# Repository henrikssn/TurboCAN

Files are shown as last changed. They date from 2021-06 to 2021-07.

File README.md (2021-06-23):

# TurboCAN

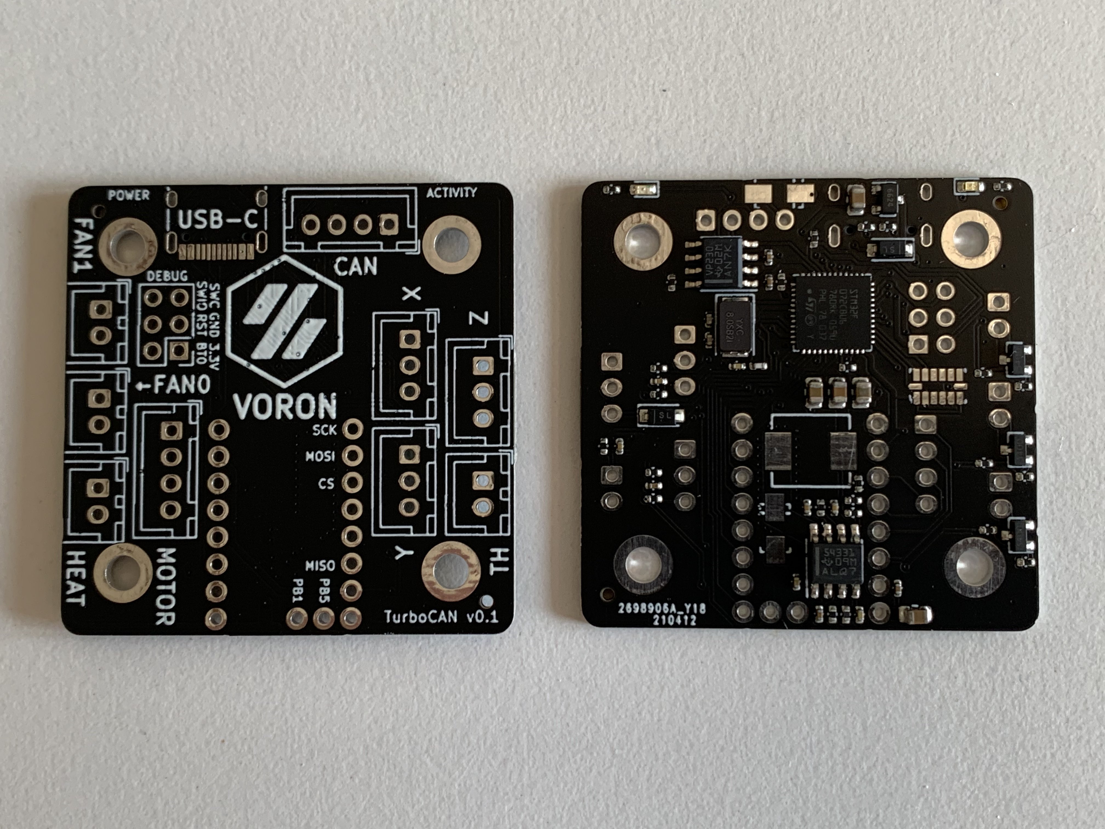
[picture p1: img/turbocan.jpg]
Image of TurboCAN board


This is the official repository for the TurboCAN controller board, designed specifically for the [Voron AfterBurner] toolhead but can also be used on similar toolheads using NEMA17 steppers. The main benefit of this board is the capability to run the toolhead over just 4 wires (CAN, +24V, Ground) which greatly simplifies the wiring in the Voron v1 and v2 models.

[Voron AfterBurner]: https://github.com/VoronDesign/Voron-Afterburner

## Features

* 1x Combined CAN-bus and 24V power port with polarity protection
* 1x ADXL345 accelerometer for use with Klipper's input shaper feature
* 1x 24V stepper stick mount and motor output
* 3x 24V MOSFET fan0/fan1/heater outputs (up to 3A)
* 2x 5V powered endstop inputs (marked X/Y), could be used for toolhead mounted endstops (microswitch or hall effect), filament runout sensor or 5V Z probe.
* 1x 24V powered endstop input (marked Z) with built-in BAT42 diode, used for inductive probe on the AfterBurner but also supports microswitch based probing (e.g. Magprobe).
* 1x Thermistor input with 4.7k pullup resistor
* 1x USB-C port
* 1x SWD debug port with BOOT0/RESET broken out
* 5V 3A buck converter (available externally on X/Y endstops) and 3.3V 200mA linear regulator (internal only)
* Power LED & Activity (PA1) LED

The board supports interfacing with Klipper both over CAN and USB-C (selectable when building the Klipper firmware).

## Use cases

The TurboCAN board is actually not only useful as a toolhead board, here are some reasons why you want more of them:

* Want even less wiring? TurboCAN fits on the back of any NEMA17 stepper, so you can mount TurboCAN boards on e.g. the A/B (or X/Y) steppers and run them over a shared CAN bus.
* Need a USB to CAN interface? TurboCAN can do USB and CAN at the same time, so you can flash CandleLight firmware and use it as a USB-CAN interface.
* Want input shaper but annoyed by the complicated SPI wiring needed for the ADXL345 board? Just use a spare TurboCAN board over USB(/CAN) instead.

## Current status

**WARNING:** While the author has a working printer running a TurboCAN v0.1 board, this project is in early development, and most likely still has undiscovered issues. Build one at your own risk!

- [x] v0.1 boards ordered
- [x] v0.1 boards testing
  - [x] LEDs
  - [x] 3.3v LDO
  - [x] SWD debug port
  - [x] USB interface
  - [x] Buck converter
  - [x] Stepper stick
  - [x] MOSFET outputs
  - [x] CAN-bus + Flashing Klipper (CAN)
  - [x] Thermistor input
  - [x] X/Y endstop inputs
  - [x] Z endstop input

## Getting started

1. Configure Klipper using `make menuconfig`:

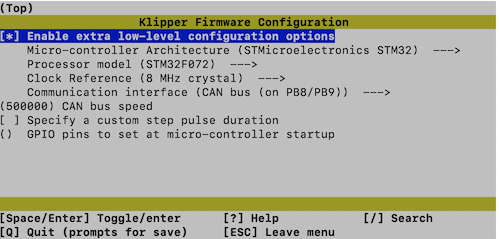
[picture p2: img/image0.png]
Klipper menuconfig


2. Put a jumper between `BOOT0` and `3.3V` and power cycle the board.

3. Flash the TurboCAN board using `make flash FLASH_DEVICE=1234:ABCD` (replace USB vendor/product, you find them with `lsusb`).

4. Connect the TurboCAN board using your favorite CAN bus interface (or use another TurboCAN board, see below).

5. Run the `klipper/scripts/canbus_query.py` command to determine the CAN address. See [Klipper docs](https://www.klipper3d.org/CANBUS.html) for more info.

6. Use the [provided Klipper config](klipper/turbocan.cfg) as a starting point.

## Changelog

### v0.2

* Errata fixes
  * LEDs are now mounted the right way.
  * R11 connected to R10/VSENSE.
  * SPI bus to the ADXL345 now have MISO/MOSI on the right pins.
  * Z probe input now has filtering and pullup resistor.
  * Reworked buck converter compensation circuitry.
  * Added CAN termination resistor.
* Added 100uF bulk capacitor for 24V to mitigate voltage fluctuations due to long cables.
* Thermistor resistor is now in 0805 package (was 0402) to simplify replacement to 1k (for PT1000 sensor).
* Improved filtering of analog power domain to reduce ADC noise.
* Replaced the heater mosfet with a more powerful AON7400A.
* Replaced the +3.3V connection to MS1 with an unpopulated resistor to give the board UART address 0 by default.
* Added optional pullup resistors to MS2/SPREAD to support standalone mode for the step stick.

## Errata

### v0.1

* LEDs are mounted backwards.
  * Workaround: Reverse them (or simply skip, they aren't essential).
* R11 not connected to R10/VSENSE.
  * Workaround: Simple to bodge as R10 is next to it.
* MISO and MOSI are swapped on the SPI bus to the ADXL345.
  * Workaround: Use software SPI.
* Z probe input lacks filtering and pullup resistor
  * Workaround: Use MCU internal pullup.
* Higher than optimal noise from the buck converter leading to noisy accelerometer readings.
  * Workaround: Doesn't need one, performance is still good enough for input shaper.
* No CAN termination resistors on-board
  * Workaround: Mount a 0603 120Ohm resistor between the H/L legs of the CAN JST-XH connector on each end of the bus.
* Thermistor readings are noisy (fluctuating 2-3C) with a PT1000 sensor
  * Workaround: Use a B3950 or replace the pullup resistor with a 1k 0.5%

## Developer Info

### Generating fabrication outputs for JLCPCB

1. Export Gerbers and drill file from pcbnew, make a zip file out of these.
2. Generate a BOM csv using `bom_csv_jlcpcb.py` from [kicad-jlcpcb-bom-plugin].
3. Generate a CPL file from pcbnew.
4. Convert the CPL file to JLCPCB format using  using `kicad_pos_to_cpl.py` from [kicad-jlcpcb-bom-plugin].

[kicad-jlcpcb-bom-plugin]: https://github.com/wokwi/kicad-jlcpcb-bom-plugin
## Attribution

Although this was designed from scratch, it was inspired by the [Huvud] board made by Pontus Borg.

[Huvud]: https://github.com/bondus/KlipperToolboard

## License

For compability with other Voron projects, all included files are licensed under the [GNU GPL-3 license].

[GNU GPL-3 license]: https://www.gnu.org/licenses/gpl-3.0.html

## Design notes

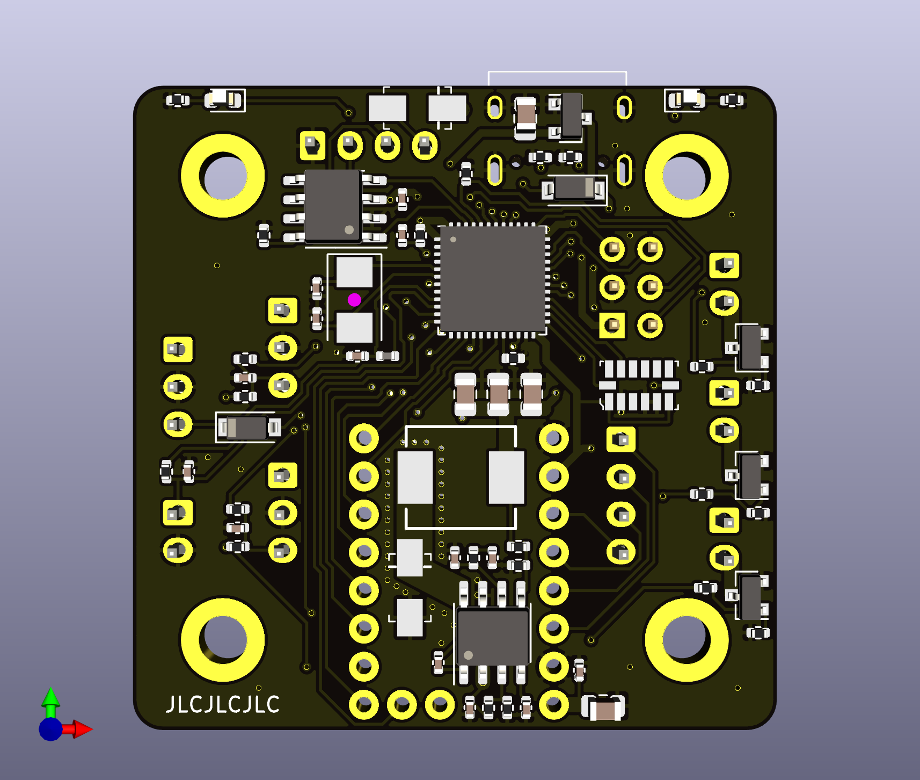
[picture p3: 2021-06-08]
hardware/png/turbocan-front.png

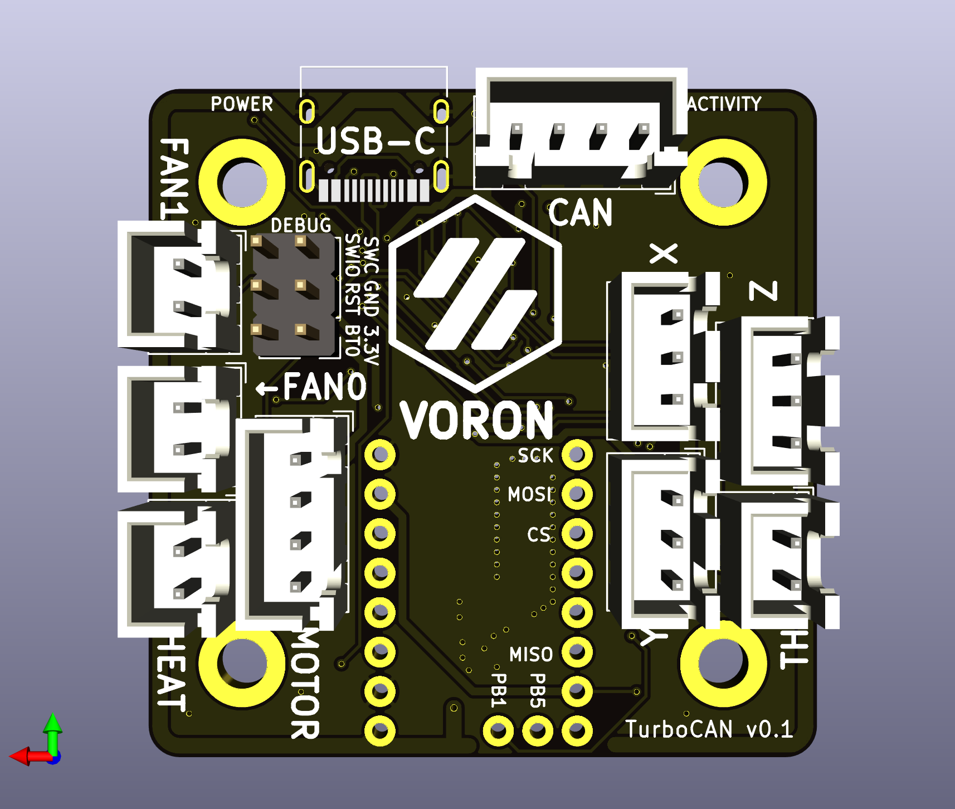
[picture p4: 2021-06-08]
hardware/png/turbocan-back.png

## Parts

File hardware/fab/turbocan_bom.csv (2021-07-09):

Comment | Designator | Footprint | LCSC Part #
10uF | C1,C5 | C_0805_2012Metric | C15850
100nF | C2,C3,C4,C9,C10,C11,C12,C17,C20,C22 | C_0402_1005Metric | C1525
10nF | C6,C19 | C_0402_1005Metric | C15195
1nF | C7 | C_0402_1005Metric | C1523
1pF | C8 | C_0402_1005Metric | C1550
22uF | C13,C14,C15 | C_0805_2012Metric | C45783
12pF | C16,C18 | C_0402_1005Metric | C1547
100uF | C21 | CP_Elec_8x10 | C59944
1uF | C23 | C_0402_1005Metric | C52923
BAT42W-V | D1 | D_SOD-123 | C8598
SS54 | D2,D3 | DO-214AC | C22452
BAT42W | D4 | D_SOD-123 | C8598
LED_Red | D5 | LED_0603_1608Metric | C2286
LED_Green | D6 | LED_0603_1608Metric | C72043
MountingHole | H1,H2,H3,H4 | MountingHole_3.2mm_M3_DIN965_Pad
USB_C_Receptacle_USB2.0 | J1 | USB_C_Receptacle_HRO_TYPE-C-31-M-12
STEPPER | J2 | JST_XH_B4B-XH-A_1x04_P2.50mm_Vertical
DEBUG | J5 | PinHeader_2x03_P2.54mm_Vertical
ENDSTOPX | J7 | JST_XH_B3B-XH-A_1x03_P2.50mm_Vertical
ENDSTOPY | J8 | JST_XH_B3B-XH-A_1x03_P2.50mm_Vertical
TH0 | J9 | JST_XH_B2B-XH-A_1x02_P2.50mm_Vertical
CAN_PORT | J10 | JST_XH_B4B-XH-A_1x04_P2.50mm_Vertical
FAN0 | J11 | JST_XH_B2B-XH-A_1x02_P2.50mm_Vertical
FAN1 | J12 | JST_XH_B2B-XH-A_1x02_P2.50mm_Vertical
HEAT | J13 | JST_XH_B2B-XH-A_1x02_P2.50mm_Vertical
PROBE | J14 | JST_XH_B3B-XH-A_1x03_P2.50mm_Vertical
6.8uH | L1 | L_SMD_7.3x6.8 | C207841
Ferrite bead | L2,L3 | L_0805_2012Metric | C1017
5.1k | R1,R2 | R_0402_1005Metric | C25905
1k | R3,R12,R13,R23,R24,R28 | R_0402_1005Metric | C11702
330k | R4 | R_0402_1005Metric | C25778
68k | R5,R6 | R_0402_1005Metric | C36871
10k | R7,R8,R10,R14,R15,R16,R20,R21,R22,R27 | R_0402_1005Metric | C25744
4.7k | R9 | R_0805_2012Metric | C17673
1.2k | R11 | R_0402_1005Metric | C25862
100 | R17,R18,R19 | R_0402_1005Metric | C25076
680 | R25 | R_0402_1005Metric | C25130
120Ohm | R26 | R_0805_2012Metric | C17437
DNP | R29,R30,R31 | R_0402_1005Metric
AP2127N-3.3 | U1 | SOT-23 | C5446
TMC2209StepStick | U2 | TMC2209StepStick
SN65HVD230 | U3 | SOIC-8_3.9x4.9mm_P1.27mm | C12084
TPS54331 | U4 | SOIC-8_3.9x4.9mm_P1.27mm | C9865
AO3400A | U5,U6 | SOT-23 | C344010
AON7400A | U7 | DFN-8-1EP_3x3mm_P0.65mm_EP1.7x2.05mm | C85734
STM32F072CBUx | U8 | QFN-48-1EP_7x7mm_P0.5mm_EP5.6x5.6mm | C92504
ADXL345BCCZ | U9 | LGA-14_3x5mm_RevA | C9667
Crystal | Y1 | Crystal_SMD_5032-2Pin_5.0x3.2mm | C115962

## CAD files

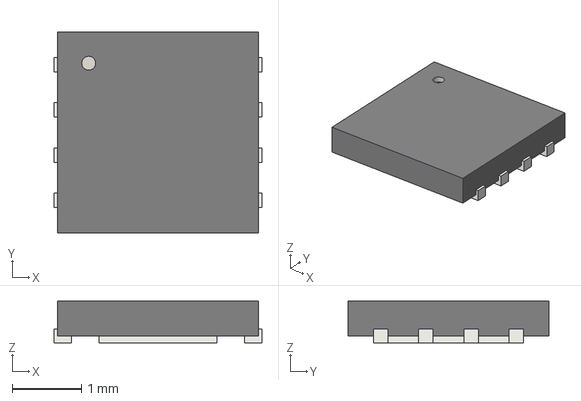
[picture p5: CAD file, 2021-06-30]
hardware/shapes3D/DFN-8-1EP_3x3mm_P0.65mm_EP1.7x2.05mm.step
3.00 x 2.90 x 0.6 mm

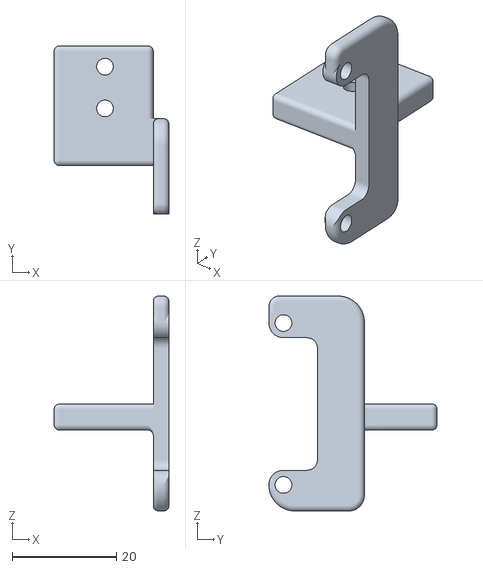
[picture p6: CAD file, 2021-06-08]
STL/Chain Anchor High.stl
22.0 x 32.2 x 41.2

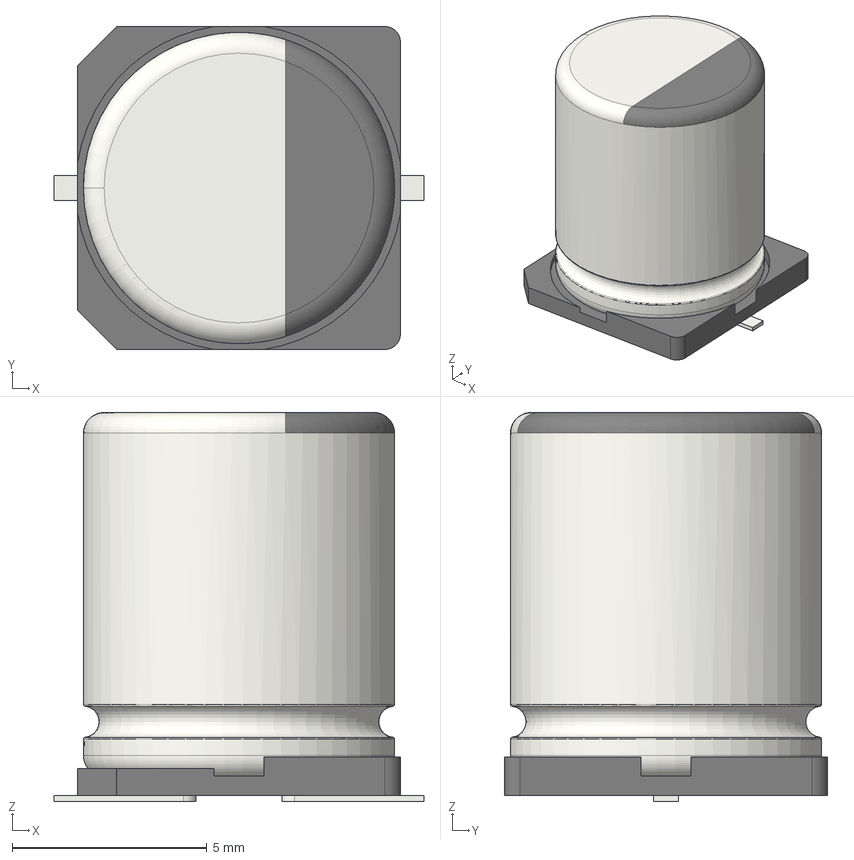
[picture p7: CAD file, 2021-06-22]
hardware/shapes3D/CP_Elec_8x10.step
9.50 x 8.30 x 10.0 mm

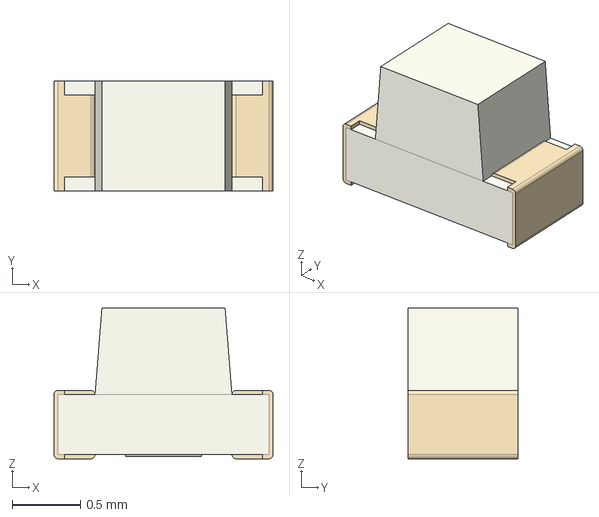
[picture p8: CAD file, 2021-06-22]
hardware/shapes3D/LED_0603_1608Metric.step
1.60 x 0.8 x 1.10 mm

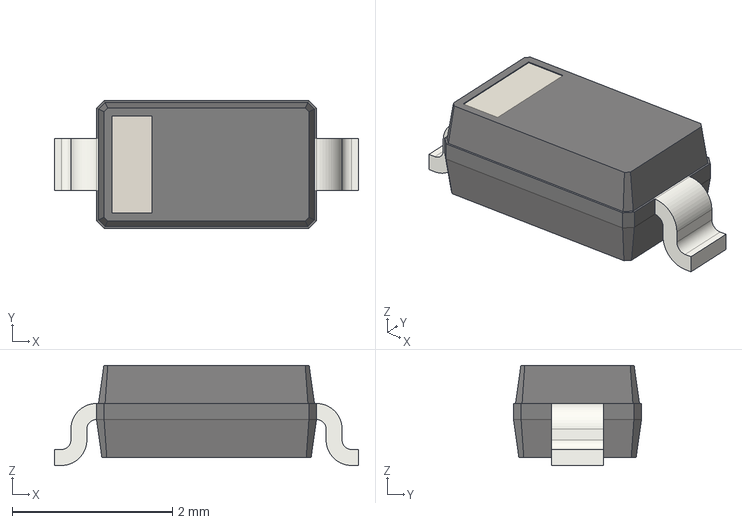
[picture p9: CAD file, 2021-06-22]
hardware/shapes3D/D_SOD-123.step
3.80 x 1.60 x 1.25 mm

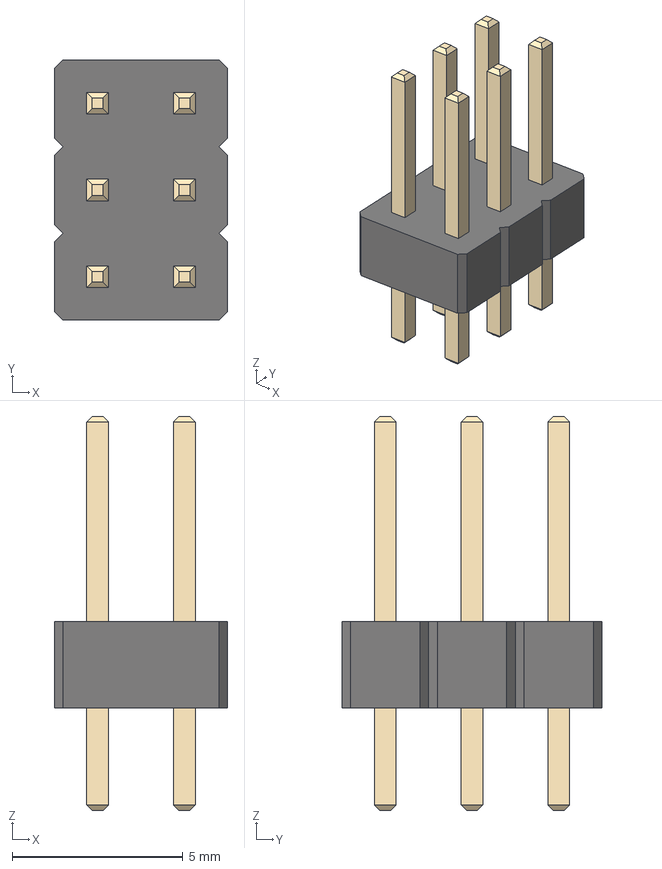
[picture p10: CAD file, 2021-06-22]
hardware/shapes3D/PinHeader_2x03_P2.54mm_Vertical.step
5.08 x 7.62 x 11.5 mm

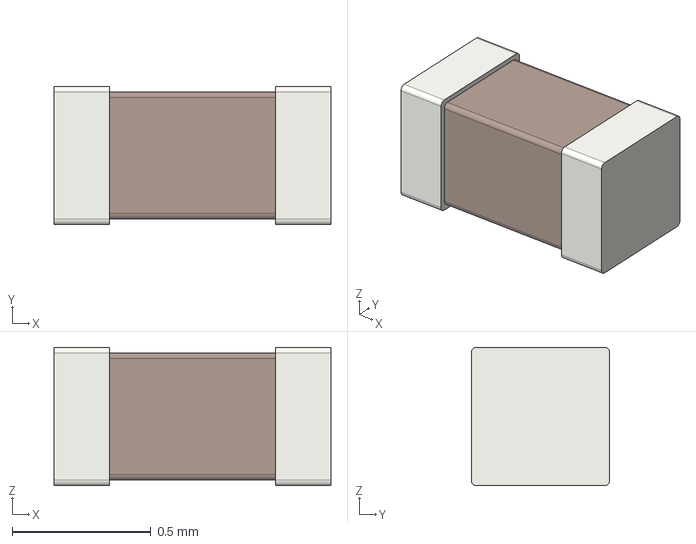
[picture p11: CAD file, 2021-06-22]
hardware/shapes3D/C_0402_1005Metric.step
1.00 x 0.5 x 0.5 mm

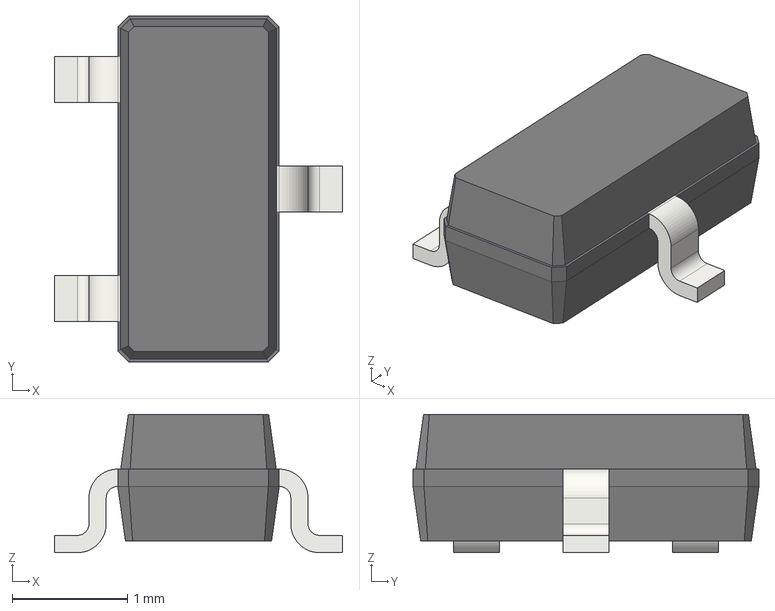
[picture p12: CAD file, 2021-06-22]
hardware/shapes3D/SOT-23.step
2.50 x 3.00 x 1.20 mm

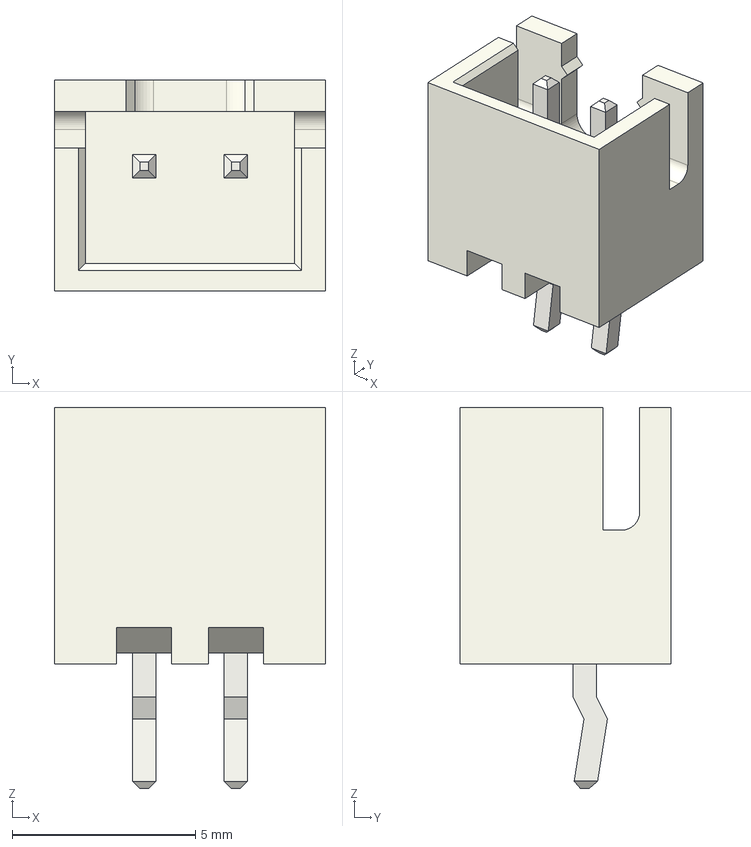
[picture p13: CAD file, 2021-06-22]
hardware/shapes3D/JST_XH_B2B-XH-A_1x02_P2.50mm_Vertical.step
7.40 x 5.75 x 10.4 mm

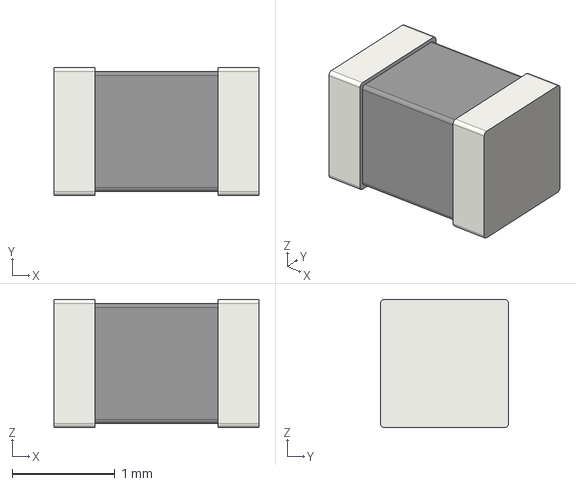
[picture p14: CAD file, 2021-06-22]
hardware/shapes3D/L_0805_2012Metric.step
2.00 x 1.25 x 1.25 mm

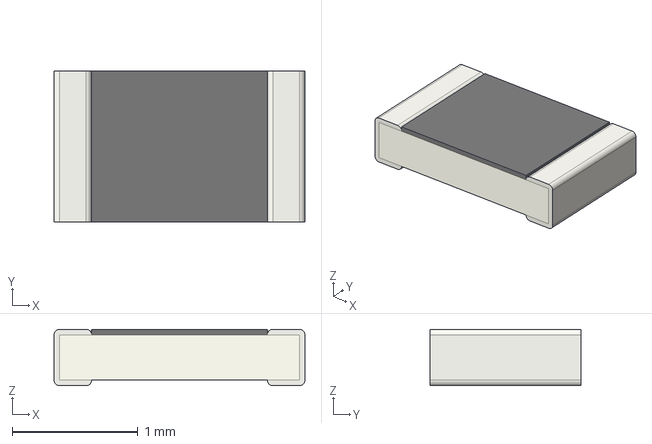
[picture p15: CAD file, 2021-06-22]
hardware/shapes3D/R_0805_2012Metric.step
2.00 x 1.20 x 0.45 mm

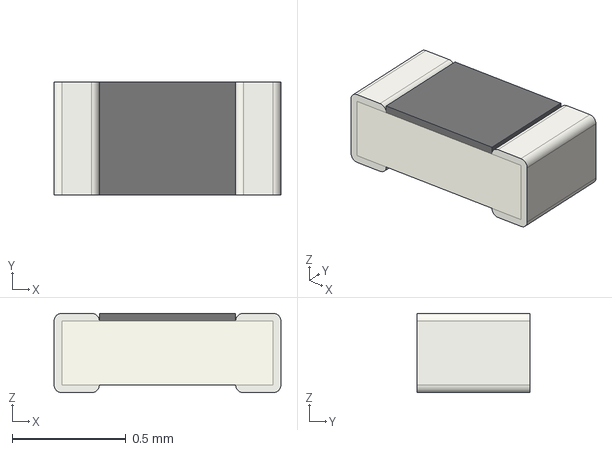
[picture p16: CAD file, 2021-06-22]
hardware/shapes3D/R_0402_1005Metric.step
1.00 x 0.5 x 0.35 mm

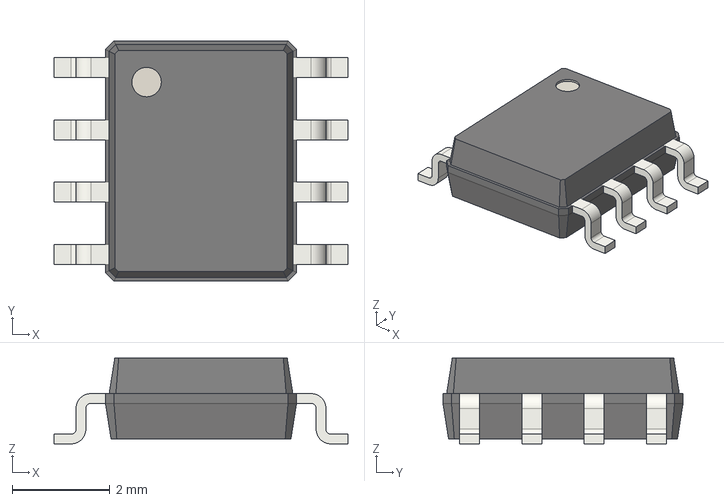
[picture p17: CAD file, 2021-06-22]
hardware/shapes3D/SOIC-8_3.9x4.9mm_P1.27mm.step
6.00 x 4.90 x 1.75 mm

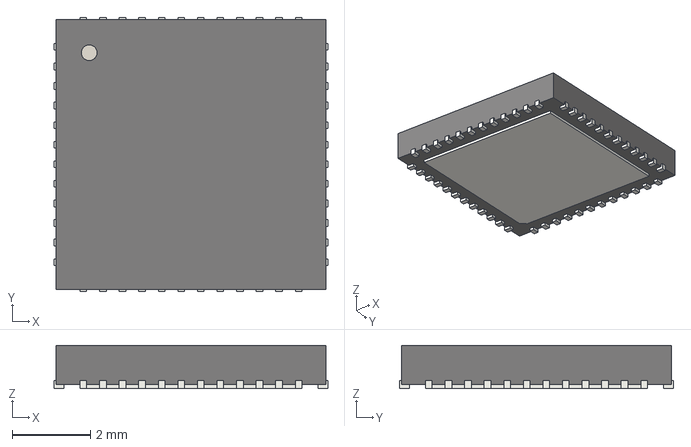
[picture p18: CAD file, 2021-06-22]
hardware/shapes3D/QFN-48-1EP_7x7mm_P0.5mm_EP5.6x5.6mm.step
7.00 x 7.00 x 1.10 mm

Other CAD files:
hardware/shapes3D/JST_XH_B4B-XH-A_1x04_P2.50mm_Vertical.step
hardware/shapes3D/JST_XH_B3B-XH-A_1x03_P2.50mm_Vertical.step
hardware/shapes3D/C_0805_2012Metric.step

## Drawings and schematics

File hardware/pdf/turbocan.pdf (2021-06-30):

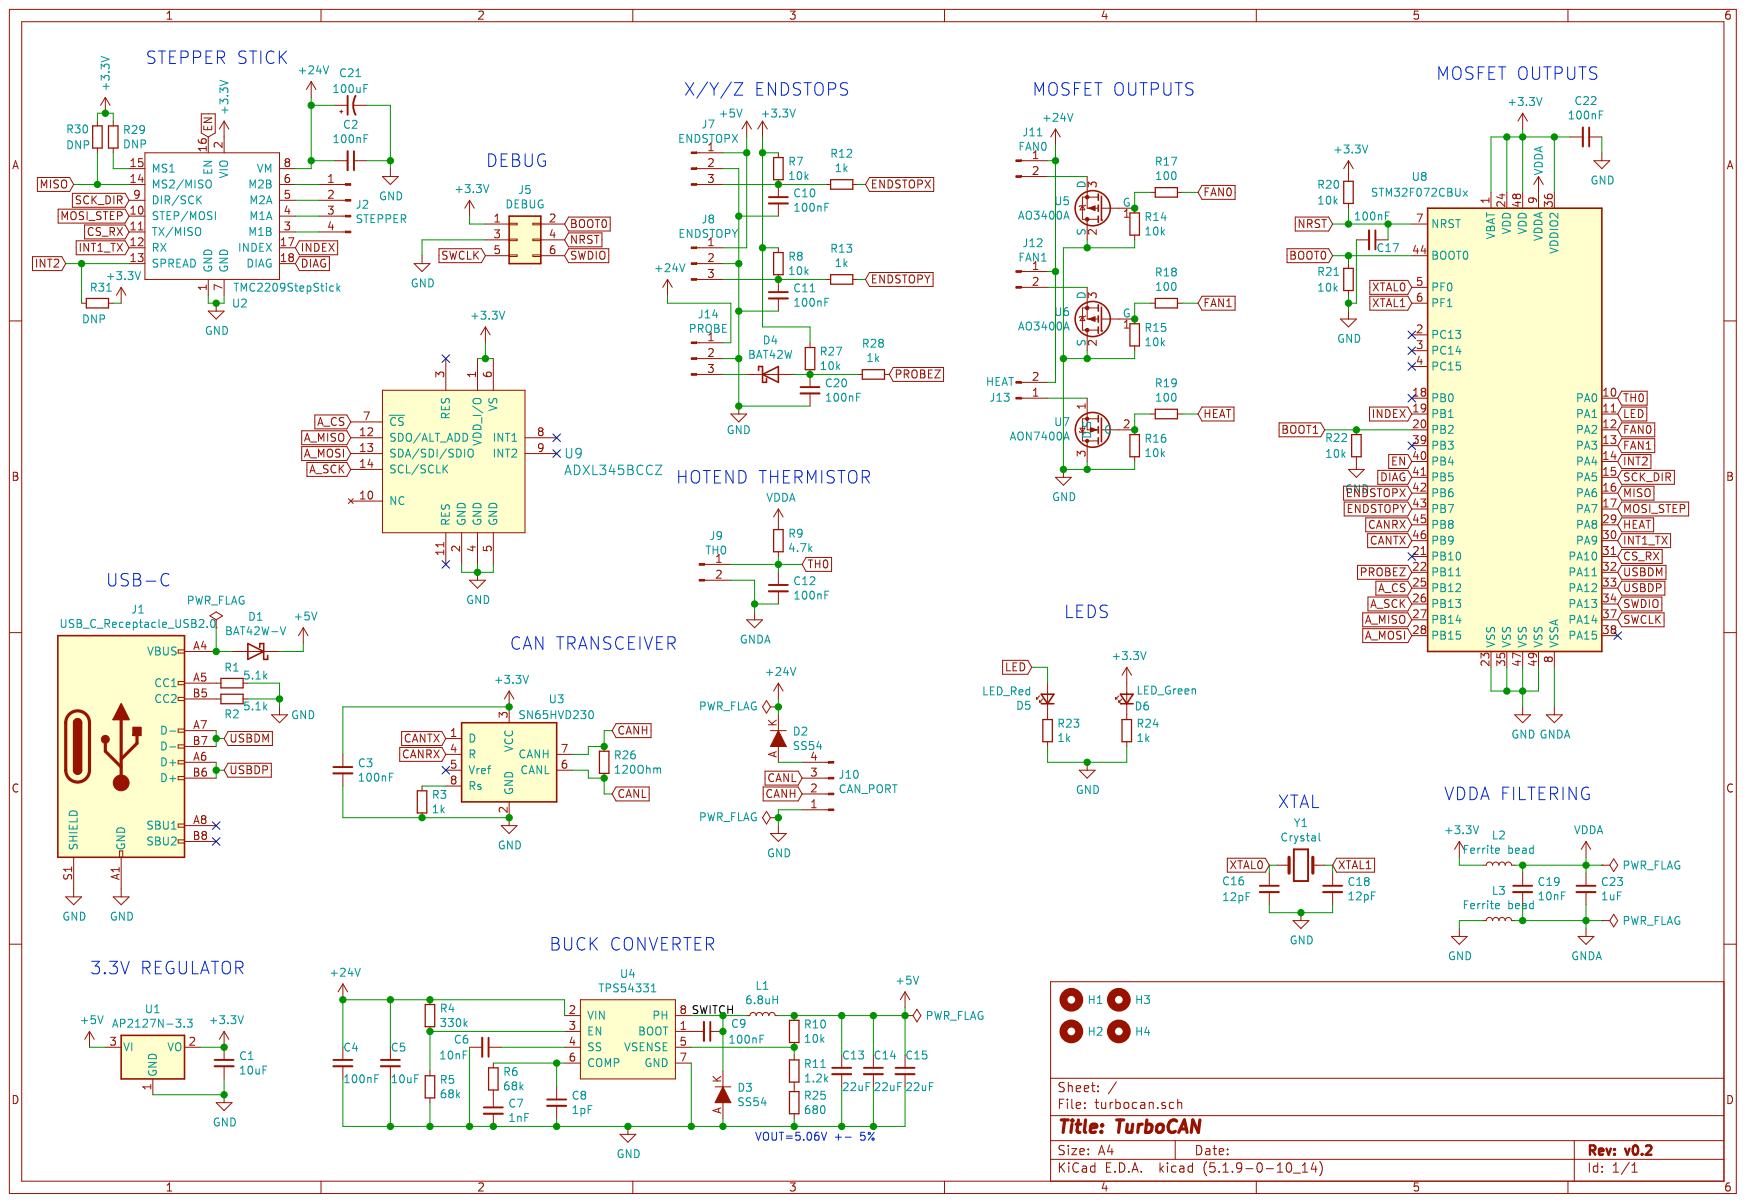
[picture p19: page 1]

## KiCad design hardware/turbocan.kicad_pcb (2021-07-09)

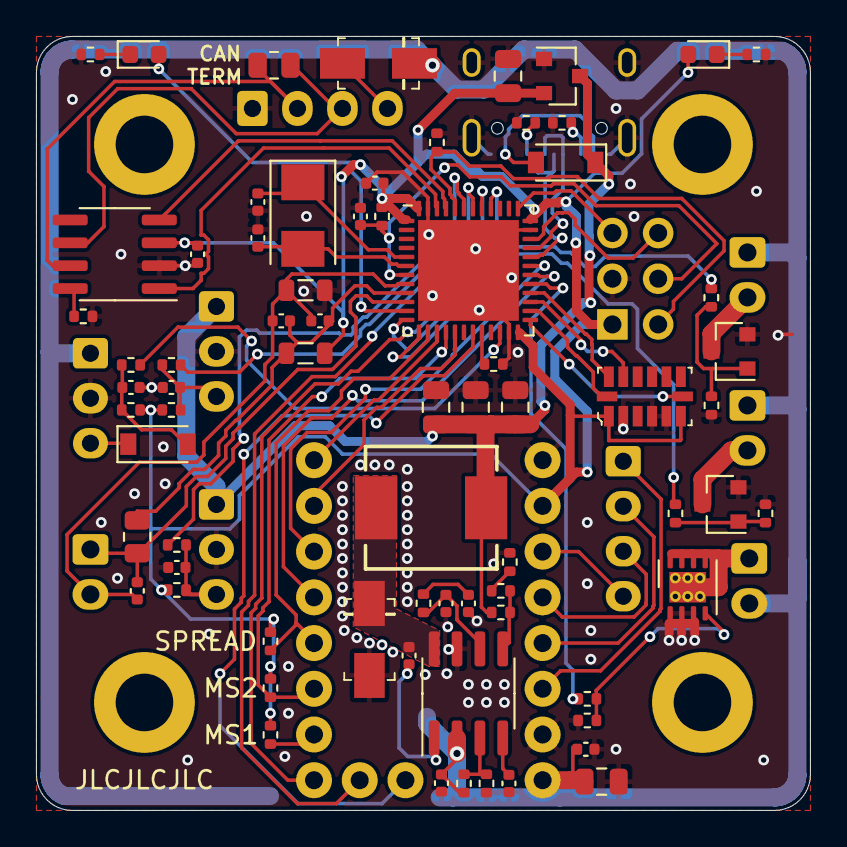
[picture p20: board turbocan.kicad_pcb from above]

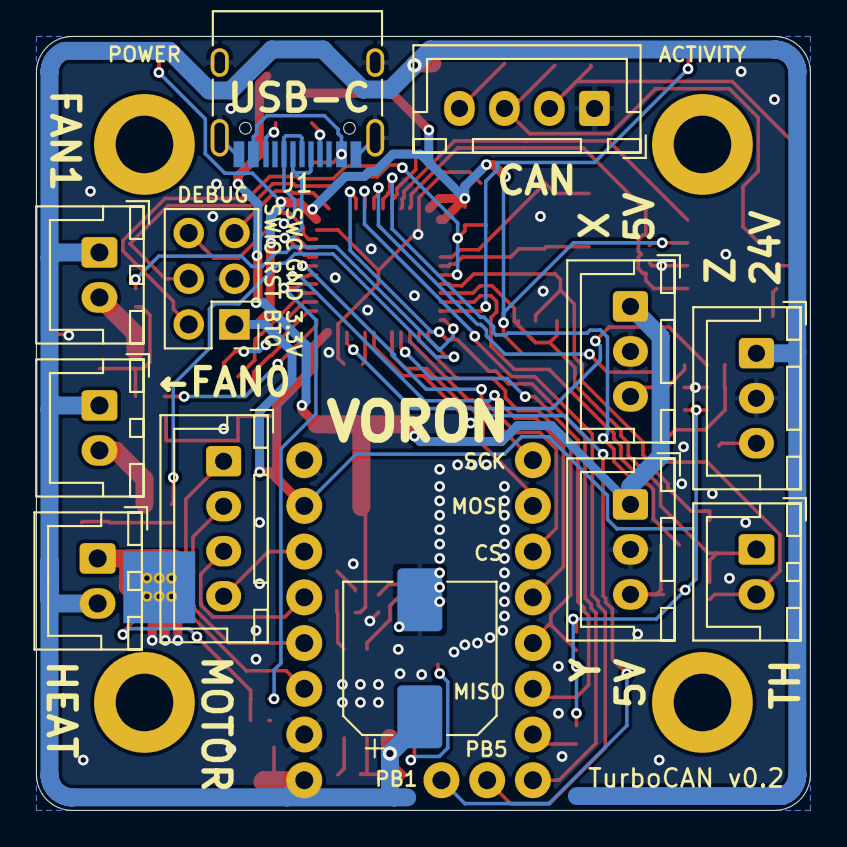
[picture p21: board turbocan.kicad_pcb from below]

Board: 2 copper layers, 43.0 x 43.0 mm, 88 parts (13 on the bottom side), 70 nets.

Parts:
C1, C5: 10uF; C_0805_2012Metric
C2, C3, C4, C9, C10, C11, C12, C17, C20, C22: 100nF; C_0402_1005Metric
C6, C19: 10nF; C_0402_1005Metric
C7: 1nF; C_0402_1005Metric
C8: 1pF; C_0402_1005Metric
C13, C14, C15: 22uF; C_0805_2012Metric
C16, C18: 12pF; C_0402_1005Metric
C21: 100uF; CP_Elec_8x10
C23: 1uF; C_0402_1005Metric
D1: BAT42W-V; D_SOD-123
D2, D3: SS54; DO-214AC
D4: BAT42W; D_SOD-123
D5: LED_Red; LED_0603_1608Metric
D6: LED_Green; LED_0603_1608Metric
H1, H2, H3, H4: MountingHole; MountingHole_3.2mm_M3_DIN965_Pad
J1: USB_C_Receptacle_USB2.0; USB_C_Receptacle_HRO_TYPE-C-31-M-12
J2: STEPPER; JST_XH_B4B-XH-A_1x04_P2.50mm_Vertical
J5: DEBUG; PinHeader_2x03_P2.54mm_Vertical
J7: ENDSTOPX; JST_XH_B3B-XH-A_1x03_P2.50mm_Vertical
J8: ENDSTOPY; JST_XH_B3B-XH-A_1x03_P2.50mm_Vertical
J9: TH0; JST_XH_B2B-XH-A_1x02_P2.50mm_Vertical
J10: CAN_PORT; JST_XH_B4B-XH-A_1x04_P2.50mm_Vertical
J11: FAN0; JST_XH_B2B-XH-A_1x02_P2.50mm_Vertical
J12: FAN1; JST_XH_B2B-XH-A_1x02_P2.50mm_Vertical
J13: HEAT; JST_XH_B2B-XH-A_1x02_P2.50mm_Vertical
J14: PROBE; JST_XH_B3B-XH-A_1x03_P2.50mm_Vertical
L1: 6.8uH; L_SMD_7.3x6.8
L2, L3: Ferrite bead; L_0805_2012Metric
R1, R2: 5.1k; R_0402_1005Metric
R3, R12, R13, R23, R24, R28: 1k; R_0402_1005Metric
R4: 330k; R_0402_1005Metric
R5, R6: 68k; R_0402_1005Metric
R7, R8, R10, R14, R15, R16, R20, R21, R22, R27: 10k; R_0402_1005Metric
R9: 4.7k; R_0805_2012Metric
R11: 1.2k; R_0402_1005Metric
R17, R18, R19: 100; R_0402_1005Metric
R25: 680; R_0402_1005Metric
R26: 120Ohm; R_0805_2012Metric
R29, R30, R31: DNP; R_0402_1005Metric
U1: AP2127N-3.3; SOT-23
U2: TMC2209StepStick
U3: SN65HVD230; SOIC-8_3.9x4.9mm_P1.27mm
U4: TPS54331; SOIC-8_3.9x4.9mm_P1.27mm
U5, U6: AO3400A; SOT-23
U7: AON7400A; DFN-8-1EP_3x3mm_P0.65mm_EP1.7x2.05mm_Thermal_Pad
U8: STM32F072CBUx; QFN-48-1EP_7x7mm_P0.5mm_EP5.6x5.6mm
U9: ADXL345BCCZ; LGA-14_3x5mm_RevA
Y1: Crystal; Crystal_SMD_5032-2Pin_5.0x3.2mm

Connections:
+3V3: C1.1, C3.1, C22.2, D6.2, J5.1, L2.1, R7.1, R8.1, R20.1, R27.1, R29.1, R30.1, R31.1, U1.2, U2.2, U3.3, U8.1, U8.24, U8.36, U8.48, U9.1, U9.6
+5V: C13.1, C14.1, C15.1, D1.1, J7.1, J8.1, L1.2, R10.1, U1.3
+24V: C2.2, C4.1, C5.1, C21.1, D2.K, J11.1, J12.1, J13.2, J14.1, R4.1, U2.8, U4.2
/SWITCH: C9.1, D3.K, L1.1, U4.8
A_CS: U8.25, U9.7
A_MISO: U8.27, U9.12
A_MOSI: U8.28, U9.13
A_SCK: U8.26, U9.14
BOOT0: J5.2, R21.1, U8.44
BOOT1: R22.1, U8.20
CANH: J10.2, R26.1, U3.7
CANL: J10.3, R26.2, U3.6
CANRX: U3.4, U8.45
CANTX: U3.1, U8.46
CS_RX: U2.11, U8.31
DIAG: U2.18, U8.41
EN: U2.16, U8.40
ENDSTOPX: R12.1, U8.42
ENDSTOPY: R13.1, U8.43
FAN0: R17.1, U8.12
FAN1: R18.1, U8.13
GND: C1.2, C2.1, C3.2, C4.2, C5.2, C6.2, C7.2, C8.2, C10.2, C11.2, C13.2, C14.2, C15.2, C16.2, C17.2, C18.2, C20.2, C21.2, C22.1, D3.A, J1.A1, J1.A12, J1.B1, J1.B12, J1.S1, J5.3, J7.2, J8.2, J10.1, J14.2, L3.1, R1.2, R2.2, R3.2, R5.2, R14.2, R15.2, R16.2, R21.2, R22.2, R23.2, R24.2, R25.2, U1.1, U2.1, U2.7, U3.2, U4.7, U5.2, U6.2, U7.1, U8.23, U8.35, U8.47, U8.49, U9.2, U9.4, U9.5
GNDA: C12.2, C19.2, C23.2, J9.2, L3.2, U8.8
HEAT: R19.1, U8.29
INDEX: U2.17, U8.19
INT1_TX: U2.12, U8.30
INT2: R31.2, U2.13, U8.14
LED: D5.2, U8.11
MISO: R30.2, U2.14, U8.16
MOSI_STEP: U2.10, U8.17
NRST: C17.1, J5.4, R20.2, U8.7
unnamed: C6.1, U4.4
unnamed: C7.1, R6.2
unnamed: C8.1, R6.1, U4.6
unnamed: C9.2, U4.1
unnamed: C10.1, J7.3, R7.2, R12.2
unnamed: C11.1, J8.3, R8.2, R13.2
unnamed: C20.1, D4.2, R27.2, R28.2
unnamed: D1.2, J1.A4, J1.A9, J1.B4, J1.B9
unnamed: D2.A, J10.4
unnamed: D4.1, J14.3
unnamed: D5.1, R23.1
unnamed: D6.1, R24.1
unnamed: J1.A5, R1.1
unnamed: J1.B5, R2.1
unnamed: J2.1, U2.6
unnamed: J2.2, U2.5
unnamed: J2.3, U2.4
unnamed: J2.4, U2.3
unnamed: J11.2, U5.3
unnamed: J12.2, U6.3
unnamed: J13.1, U7.3
unnamed: R3.1, U3.8
unnamed: R4.2, R5.1, U4.3
unnamed: R10.2, R11.1, U4.5
unnamed: R11.2, R25.1
unnamed: R14.1, R17.2, U5.1
unnamed: R15.1, R18.2, U6.1
unnamed: R16.1, R19.2, U7.2
unnamed: R29.2, U2.15
PROBEZ: R28.1, U8.22
SCK_DIR: U2.9, U8.15
SWCLK: J5.5, U8.37
SWDIO: J5.6, U8.34
TH0: C12.1, J9.1, R9.2, U8.10
USBDM: J1.A7, J1.B7, U8.32
USBDP: J1.A6, J1.B6, U8.33
VDDA: C19.1, C23.1, L2.2, R9.1, U8.9
XTAL0: C16.1, U8.5, Y1.1
XTAL1: C18.1, U8.6, Y1.2

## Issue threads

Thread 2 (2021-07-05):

Heater always on - MOSFET source and drain swapped.

robets, 2021-07-05:
I believe after #76e391446151732316c39055638c21bfe2827c88 the heater MOSFET source and drain got swapped. The symbol is upside down on the schematic, so it matches the fan drivers but drain and source are opposite in the symbol. Had some boards built at #58484556917e8c7f926e563aec05edcaa463c25e and the heater is always active.

Working on a PR to fix it up but wanted to post an issue since it affects the heater. I'm not very fluent with Kicad, so it might take me a little while.

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

henrikssn, 2021-07-08:
Ouch, thanks for contributing this back! I'll try to take a look at the PR later today.

Closed 2021-07-09.

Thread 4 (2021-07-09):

Improve power handling of the CAN port reverse polarity protection

henrikssn, 2021-07-09:
Capturing this discussion from #3:

> As a side note, the power handling increase going from the AO3400A to AON7400A is probably lost due to the SS54 diode on the power input being limited to 5A. Using another AON7400A could be suitable for reverse polarity protection instead of the diode. BOM cost increase would be fairly small since the extended part cost of the AON7400A is already done by using it once.

henrikssn, 2021-07-10:
@robets The main reason for replacing the AO3400A was safety, it failed short for me with a 60W (2.5A) heater on it and MCU temp at ~100C, I'd like more margin than that. If the SS54 diode fails, then it is much less serious.

Still, the SS54 generates ~2.5W of heat at 5A which would be quite a power dissipation problem (likely won't work) so I think it is a good improvement to replace it with a AON7400A mosfet. It is a bit tricky to make it fit though, and we would need some circuitry (maybe a zener or resistor voltage divider?) for limiting gate voltage (please select something from JLCPCB's basic components).

Another option is to simply remove it, while it is nice it might cause more issues than it solves.

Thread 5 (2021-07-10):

Is there no klipper config to set usb only?

johwanghee, 2021-07-10:
Is there no klipper config to set usb only?

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
USB doesn't work with this

henrikssn, 2021-07-11:
Hmm, this might need fixing on the Klipper side, USB is connected to the standard PA11/PA12 pins.

You could try using the stm32f042 menu option in the meanwhile, it is close enough to still work IIRC. You should select "USB on PA11/PA12".

henrikssn, 2021-07-11:
This line should include `STM32_F072`: https://github.com/KevinOConnor/klipper/blob/f24210054a2b263e7a73df1356c77b222851c0a1/src/stm32/Kconfig#L73

johwanghee, 2021-07-12:
```
config HAVE_STM32_USBFS
    bool
    default y if MACH_STM32F103 || MACH_STM32F042 || MACH_STM32F070 || MACH_STM32F072
```
After fixing the Klipper source, the USB interface is connected.
However, since this is a Klipper issue, I will close this issue.

Closed 2021-07-12.

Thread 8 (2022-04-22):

Change lcsc part number for position c21

XBoxxyX, 2022-04-22:
C487384   part #.   8x10 footprint.  NEW

C59944     part #.  10x10 footprint.   Old

both fit  but c59944 is very tight

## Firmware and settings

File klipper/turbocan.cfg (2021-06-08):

[extruder]
step_pin: turbocan0:PA7
dir_pin: turbocan0:PA5
enable_pin: !turbocan0:PB4
microsteps: 8
rotation_distance: 33.500
nozzle_diameter: 0.400
filament_diameter: 1.750
heater_pin: PA8 # Heat
sensor_pin: PA0 # TH
sensor_type: PT1000
control: pid
pid_Kp: 22.2
pid_Ki: 1.08
pid_Kd: 114
min_temp: 0
max_temp: 500

[tmc2209 extruder]
uart_pin: ^turbocan:PA4
uart_address: 1

[fan]
pin: turbocan0:PA2

[heater_fan hotend_fan]
pin: turbocan0:PA3
shutdown_speed: 0

[output_pin activity_led]
pin: PA1

[mcu turbocan0]
canbus_uuid: 1234567890AB

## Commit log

2021-06-08 Public release
    [Chain Anchor High.stl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]
2021-06-22 Make the KiCAD files standalone
    [CP_Elec_8x10.step, C_0402_1005Metric.step, C_0805_2012Metric.step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]
2021-06-22 Replace heater mosfet
    [turbocan.kicad_pcb, turbocan.sch]
2021-06-23 Fix typo in README
    [turbocan.sch]
2021-06-23 Replace pullup on MS1 with unpopulated resistor
    [turbocan.kicad_pcb, turbocan.sch]
2021-06-23 Also add optional pullup resistors on MS2 and SPREAD
    [turbocan.kicad_pcb, turbocan.sch]
2021-06-30 Fix orientation of LEDs/C21 and update C8 to 1pF
    [DFN-8-1EP_3x3mm_P0.65mm_EP1.7x2.05mm.step, turbocan.kicad_pcb, turbocan.sch]
2021-06-30 Regenerate fabrication outputs
    [turbocan-B_Cu.gbr, turbocan-B_Mask.gbr, turbocan-B_Paste.gbr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]
2021-07-05 Swap drain and source on heater MOSFET.
    [turbocan.kicad_pcb, turbocan.sch]
2021-07-06 Regenerate fabrication files
    [turbocan-B_Cu.gbr, turbocan-B_Mask.gbr, turbocan-B_Paste.gbr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]
2021-07-08 Add thermal pad and vias for heater MOSFET.
    [turbocan-B_Cu.gbr, turbocan-B_Mask.gbr, turbocan-B_Paste.gbr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]

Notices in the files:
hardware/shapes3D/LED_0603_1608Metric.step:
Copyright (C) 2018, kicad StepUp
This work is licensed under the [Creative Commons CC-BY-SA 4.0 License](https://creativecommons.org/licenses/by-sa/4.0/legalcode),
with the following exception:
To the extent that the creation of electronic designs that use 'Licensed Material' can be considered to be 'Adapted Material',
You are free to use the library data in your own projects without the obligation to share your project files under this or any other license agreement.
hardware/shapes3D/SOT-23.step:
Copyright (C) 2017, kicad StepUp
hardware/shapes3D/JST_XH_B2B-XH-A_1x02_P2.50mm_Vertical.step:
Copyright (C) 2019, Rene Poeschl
